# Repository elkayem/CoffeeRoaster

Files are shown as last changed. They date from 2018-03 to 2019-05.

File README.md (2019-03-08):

# COFFEE ROASTER

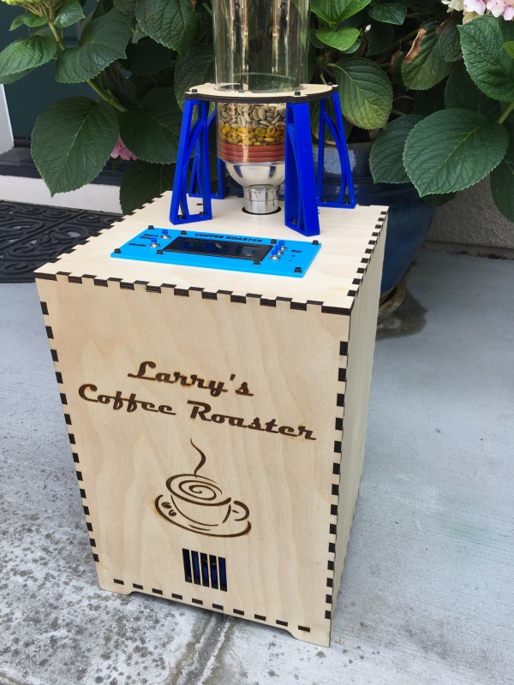
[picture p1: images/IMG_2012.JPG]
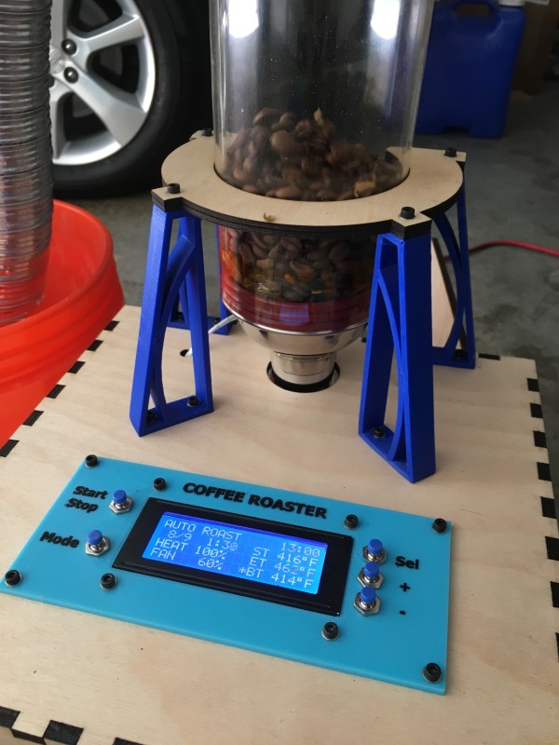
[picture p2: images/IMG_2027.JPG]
 

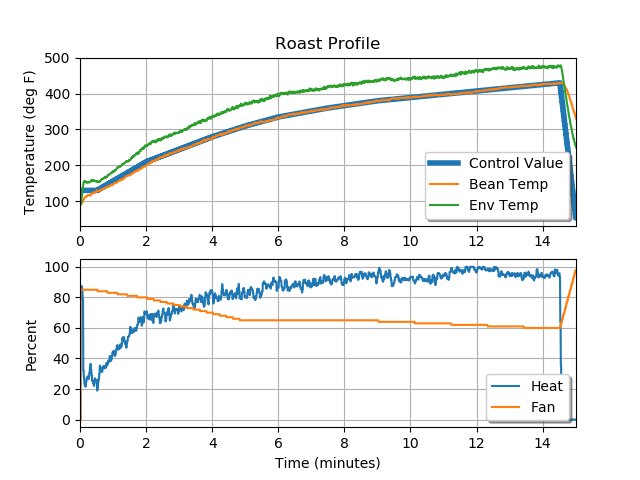
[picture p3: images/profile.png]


This repository contains the code for a PID controlled coffee roaster, run on a Teensy 3.5/3.6 development board.

A quick summary of the features:
* *Auto Mode* which will control the temperature (bean or environment) and fan speed to a settable profile.  
* *Manual Mode* where temperature and fan speed can be controlled in real time.
* Measured temperatures, set value, fan speed, and heater duty cycle saved to an SD card as a CSV file at 2 Hz while roasting.  See image above showing data from a roast.  I've also included a python script used to plot this data from the SD card.  The script requires the python module "matplotlib".  
* DC Fan PWM control.  (The MOSFET on the PCB can handle quite a bit of current.  I am using a 22 Amp, 260 Watt fan, and the MOSFET has additional headroom beyond that).    
* The roasting profile can be set as a sequence of up to 9 segments.  The set temperature and fan speed are linearly interpolated from one segment to the next.  This profile can be set and saved to EEPROM via the LCD screen interface.  
* Separate tuneable PID values for the environment temperature and bean temperature.  A tuning mode for each controller is available allowing one to monitor the step response and tune the gains in real time.
* (Optional) interface with [Artisan Roaster Scope](https://artisan-scope.org/).  The roast can be logged by Artisan in Auto or Manual mode, or even have Artisan control the set temperature and fan speed in Manual mode.  

I loosely based my roaster build off of a few of the fluid bed roasters over at the Home Roaster's forum using a Pyrex Bake-A-Round baking tube and inverted cocktail shaker lid.  For example, see Old Gear Head's fluid bed roaster design at: https://forum.homeroasters.org/forum/viewthread.php?thread_id=2207.   

Here are the parts needed for the electronics board:
* PCB (Order using gerber files in Eagle directory, or ask me and I'll send you one for a small amount.  Alternatively, the electronics can be soldered to a stripboard)
* Teensy 3.5 (or 3.6), $24.25 from pjrc.com + MicroSD card
* 2x MAX31855KASA+ thermocouple ICs ($5 each)
* 4x SMD ferrite beads (I used 470 ohms 0805 package)
* 3x BSS138 MOSFET transistors
* IRLB8721PBF MOSFET + heat sink (very important!!)
* 2N3904 transistor
* SB1245 Schottky diode
* 7805 5V regulator 
* Various resistors and capacitors (see schematic in Eagle directory)

Here are the additional parts I used:
* 20x4 character I2C LCD screen ($9 on eBay)
* Two K-type thermocouples
* Metal thermocouple probe shield (e.g., look for the 5mm x 50 mm thermocouple probe from Uxcell on Amazon, and cut off the end of the metal shield)
* Fotek SSR-40 DA Solid State Relay + Heat Sink ($12.50 on eBay)
* 12V, 25A power regulated switching power supply ($19 at eBay)
* Pyrex Bake-A-Round baking tube ($20 at eBay)
* Lid from Winco 16-oz coctail shaker, 1.5" and 3.5" diam ($7.50 at Amazon)
* 1.5" x 12" chrome tube ($10 at Amazon)
* HAS-043K 1700 Watt heating element ($22 at Amazon)
* Airhead "Air Pig" 12V, 22 Amp air pump ($42 at Amazon)
* 340 Silicone O-Rings 3.5" diam

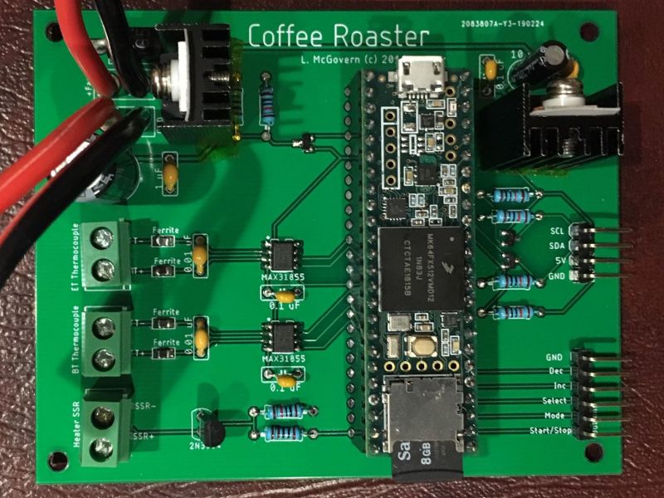
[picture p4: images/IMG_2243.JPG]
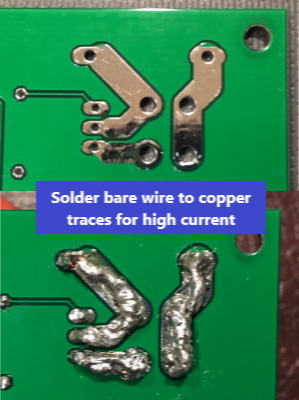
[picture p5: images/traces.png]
  

A schematic and PCB design (see Eagle folder) is included in this repository.  The Gerber files can be uploaded to a PCB manufacturer (e.g., JLCPCB, SchenZhen2U, or Seeed Studio), typically for a few dollars a board and a minimum order of 5-10 boards.  Alternatively, contact me and I can send you one (without components) at cost plus shipping.  The electronics can also be soldered to a breadboard.  If using a breadboard, you will also need two MAX31855 breakout boards from Adafruit, as well as a logic level converter for the I2C LCD communication.

The DC motor is driven by the 12V power supply, with PWM speed control from the microcontroller.  It is vitally important that a few small capacitors be soldered directly to the motor leads to reduce voltage noise on the DC power, otherwise the inevitable voltage spikes from the DC motor will reset the microcontroller in the middle of your roast.  Not good!  I used a 22 nF capacitor across the leads, and then two 10 nF capacitors from each lead directly to the motor housing.   

The 12V, 22 Amp DC motor I used draws a lot of current, so be sure to use beefy wires (e.g., 14 AWG) all the way to the MOSFET.  Be sure to use a heat sink on the IRLB8721PBF MOSFET.  The wide traces on the back of the PCB are inadequate to handle 22A.  I recommend laying down a heavy layer of solder directly to these traces.  Better yet, solder exposed 14 AWG wire directly to the traces.  See photos above.

I enclosed the DC motor in my own 3D printed case and threw away the pig shaped case on the Airhead "Air Pig".  I've included the 3D printed case model in this repository, which encloses the motor and is sealed with a 3.5" O-ring.  I'm sure the pig shaped case would work too, but don't use the corrugated hose which produces too much drag.  

Two temperature measurements are used.  I placed the Environment Temperature thermocouple close to the center of the chamber in the line of fire of the hot air, and the Bean Temperature probe off to the side and blocked from the upcoming air.  A metal thermocouple shield is used to hold the probes in place.  I purchased a thermocouple probe from Uxcell on Amazon that came with a metal shield, and sawed off the end of the metal shield.  I have included a photograph below showing the thermocouple placement, and a drawing as well.  The bean temperature thermocouple and wires are taped to the top of the thermocouple metal shield using Kapton tape, which allows this thermocouple to register the temperature of the beans descending along the side of the shaker lid, and outside of the stream of hot air.  

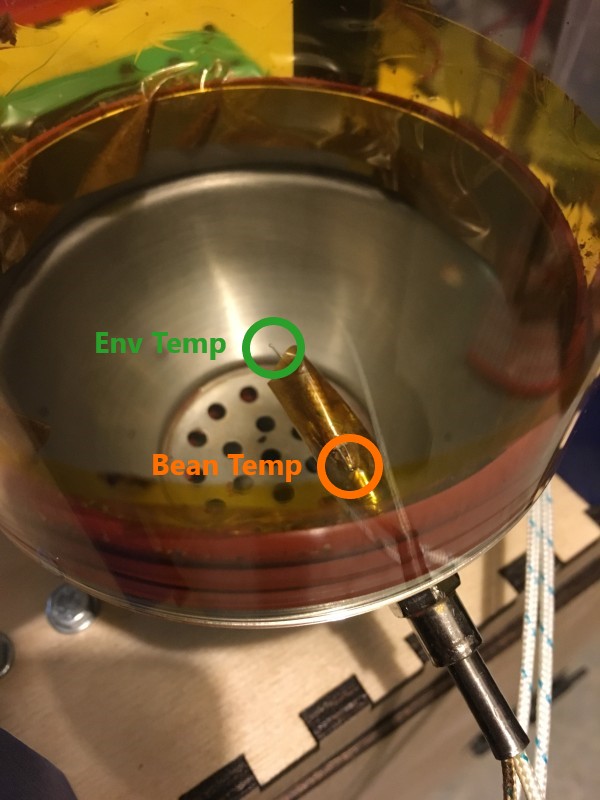
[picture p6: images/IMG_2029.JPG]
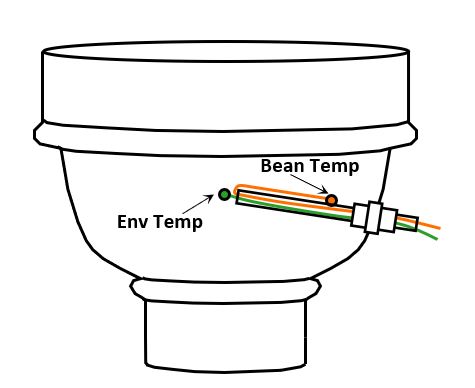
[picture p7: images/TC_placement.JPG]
 

I have also included a few 3D printed parts I used, which may be useful.  This repository includes a front panel for the LCD screen, and also the buttresses to hold the Bake-A-Round vertical. 

The plans for a 1/4" ply laser cut case are also included if you have access to a laser cutter.  Or build your own!  

# Artisan Roaster Scope Instructions
Artisan is not required for this roaster, as the Teensy firmware can already track a stored profile and save the roast data to an SD card without an external interface.  I still highly recommend Artisan as it includes additional visual analysis tools. 

**Important Note:** The USB port 5V power *must* be disconnected before attempting to interface with Artisan. There are several ways to do this, described at https://www.pjrc.com/teensy/external_power.html.  The simplest way is to disconnect the 5V pads apart on the bottom of the Teensy board.  I chose a different method in my roaster.  My roaster has a USB panel mount on the outside of the case, with an internal USB cable going from the panel mount to the Teensy.  Since this cable is permanently isntalled inside my case, I chose to clip the red wire inside the cable, sealing off the cut wire with shrink tube to prevent a short.  This avoids the need to modify the Teensy itself.

Coffee Roaster uses the same Artisan communication protocol as a TC4.  To use this Teensy code with Artisan, set up the device as a TC4 in Config>Device on the ET/BT tab.  Check the "Control" and "PID Firmware" checkboxes.  On the Extra Devices tab, set up the ArduinoTC4_34, ArduinoTC4_56 (Label 1 = Heater, Label 2 = Fan), and ArduinoTC4_78 (Label 1 = SV, Label 2 = Ambient).  Check the LCD 1, LCD 2, Curve 1, and Curve 2 checkboxes for ArduinoTC4_56 and _78, but uncheck for _34.  The YouTube video [Artisan Roaster Scope - Setup for TC4](https://youtu.be/0-Co-pXF2NM) walks through the setup procedure.

The above steps are sufficient for logging your roast with Artisan.  To control the roast using Artisan, check out the YouTube video [Artisan Roaster Scope - TC4 PID Control](https://youtu.be/ykuUCXhGAC4).  This video has four parts.  The two parts labeled "Background Follow TC4 PID" and "Ramp/Soak Profile TC4 PID" can be used with this code.  The "Artisan PID" variants are not currently supported.  

If using Artisan to control your roaster, you will also need to set up the DC Fan control. To do this, open the Config>Events dialog, change the first Event name to Fan, go to the Sliders tab, and set the Fan Action to Serial Command, and add the command "DCFAN;{}" to the selection box, without the quotes.  

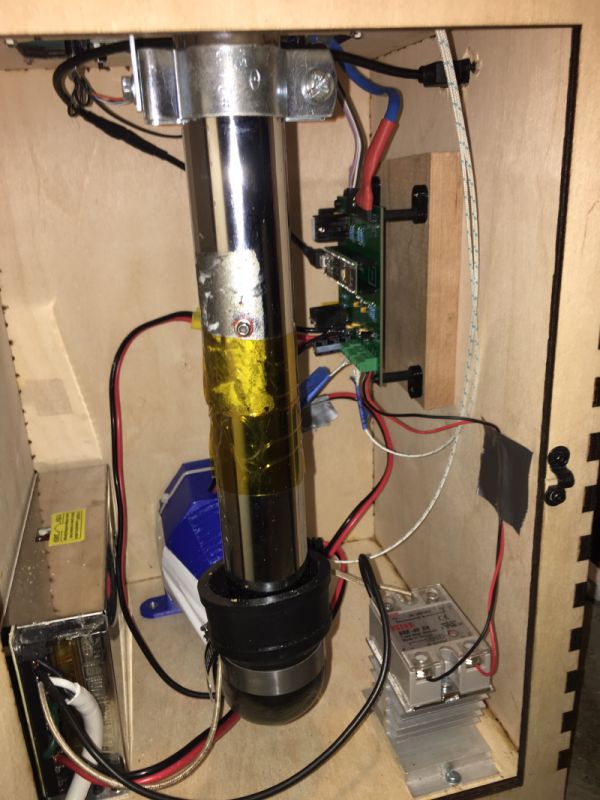
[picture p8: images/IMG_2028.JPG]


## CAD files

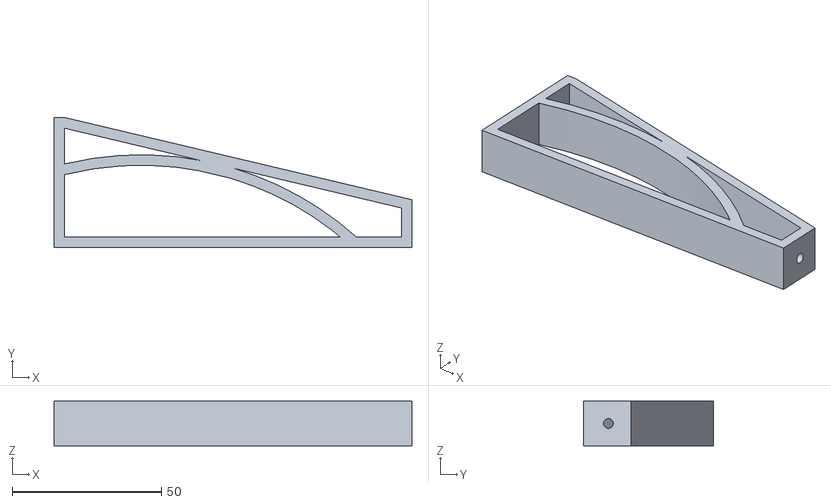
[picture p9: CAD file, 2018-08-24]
3D Printed Parts/buttress.stl
120.0 x 43.6 x 15.0

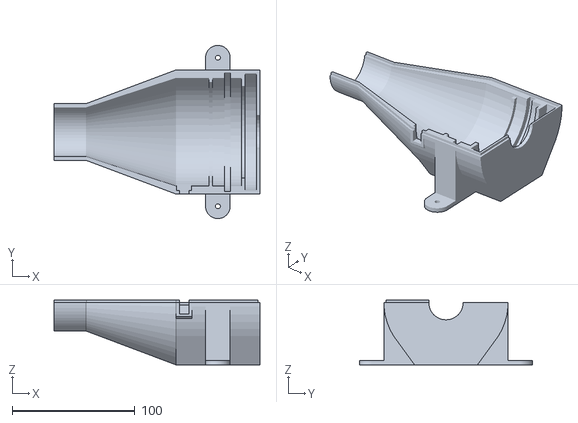
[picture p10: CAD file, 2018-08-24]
3D Printed Parts/fan_case_bottom.stl
167.5 x 140.8 x 52.5

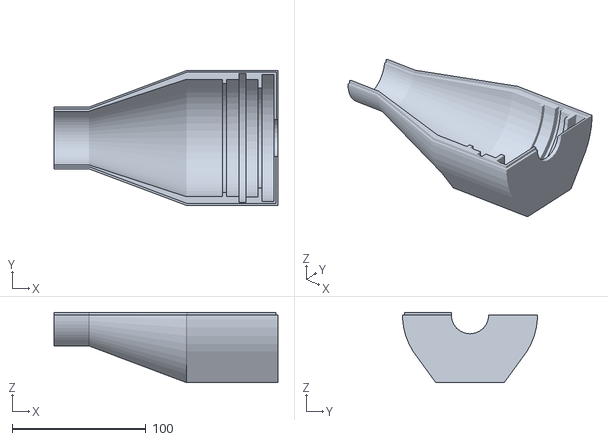
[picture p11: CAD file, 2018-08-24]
3D Printed Parts/fan_case_top.stl
167.5 x 100.8 x 52.5

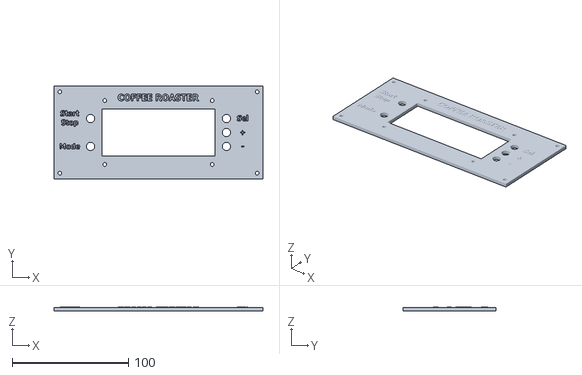
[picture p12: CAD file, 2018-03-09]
3D Printed Parts/panel.stl
180.0 x 80.0 x 3.45

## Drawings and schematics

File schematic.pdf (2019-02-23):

# BSS138 BSS138

# 1K ¹²³⁴⁵⁶⁷⁸⁹

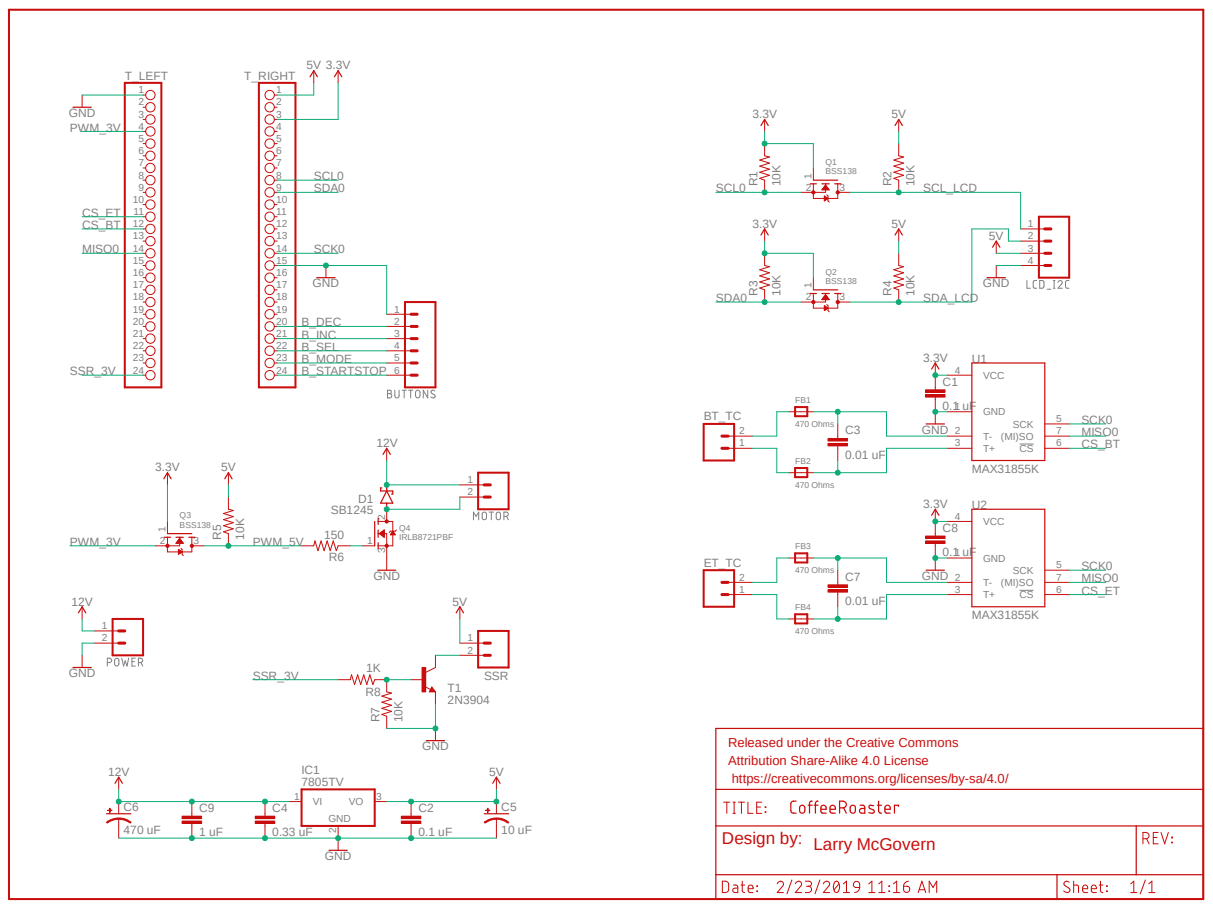
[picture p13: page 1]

Released under the Creative Commons
Attribution Share-Alike 4.0 License
https://creativecommons.org/licenses/by-sa/4.0/

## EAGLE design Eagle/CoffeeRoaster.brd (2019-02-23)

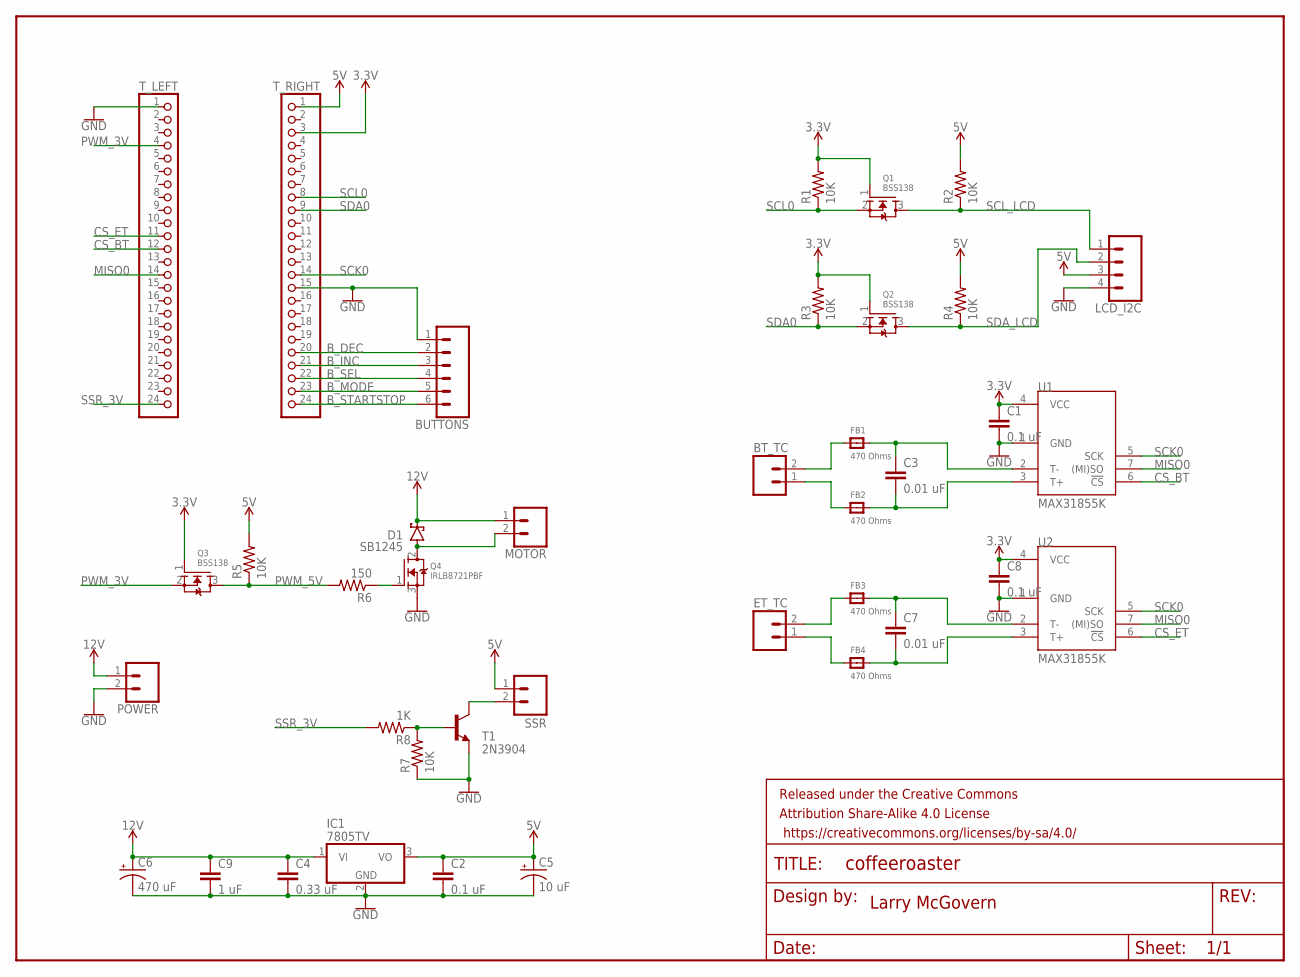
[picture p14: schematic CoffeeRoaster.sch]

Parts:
BT_TC: M025MM; SCREWTERMINAL-5MM-2
BUTTONS: CONN_06SILK_FEMALE_PTH; 1X06
C1, C2, C8: 0.1 uF; C050-025X075
C3, C7: 0.01 uF; C050-025X075
C4: 0.33 uF; C050-025X075
C5: 10 uF; E2,5-6
C6: 470 uF; E5-10,5
C9: 1 uF; C050-025X075
D1: SB1245; DO201T15
ET_TC: M025MM; SCREWTERMINAL-5MM-2
FB1, FB2, FB3, FB4: 470 Ohms; _0805
FRAME1: FRAME-LETTER; CREATIVE_COMMONS
IC1: 7805TV; TO220V
LCD_I2C: CONN_04; 1X04
MOTOR: CONN_02PTH4; 1X02_XTRA_BIG
POWER: CONN_02PTH4; 1X02_XTRA_BIG
Q1, Q2, Q3: BSS138; SOT23
Q4: IRLB8721PBF; TO220V
R1, R2, R3, R4, R5, R7: 10K; 0207/10
R6: 150; 0207/10
R8: 1K; 0207/10
SSR: M025MM; SCREWTERMINAL-5MM-2
T1: 2N3904; TO92
T_LEFT: PINHD-1X24; 1X24
T_RIGHT: PINHD-1X24; 1X24
U1, U2: MAX31855K; SO08

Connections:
3.3V: C1.1, C8.1, Q1.1 (G), Q2.1 (G), Q3.1 (G), R1.2, R3.2, T_RIGHT.3, U1.4 (VCC), U2.4 (VCC)
5V: C2.1, C5.+, IC1.3 (VO), LCD_I2C.3, R2.2, R4.2, R5.2, SSR.1, T_RIGHT.1
12V: C4.1, C6.+, C9.1, D1.C, IC1.1 (VI), MOTOR.1, POWER.1
B_DEC: BUTTONS.2, T_RIGHT.20
B_INC: BUTTONS.3, T_RIGHT.21
B_MODE: BUTTONS.5, T_RIGHT.23
B_SEL: BUTTONS.4, T_RIGHT.22
B_STARTSTOP: BUTTONS.6, T_RIGHT.24
CS_BT: T_LEFT.12, U1.6 (!CS)
CS_ET: T_LEFT.11, U2.6 (!CS)
GND: BUTTONS.1, C1.2, C2.2, C4.2, C5.-, C6.-, C8.2, C9.2, IC1.2 (GND), LCD_I2C.4, POWER.2, Q4.3 (S), R7.1, T1.3 (E), T_LEFT.1, T_RIGHT.15, U1.1 (GND), U2.1 (GND)
MISO0: T_LEFT.14, U1.7 ((MI)SO), U2.7 ((MI)SO)
MOT_NEG: D1.A, MOTOR.2, Q4.2 (D)
unnamed: Q4.1 (G), R6.1
unnamed: BT_TC.2, FB1.1
unnamed: ET_TC.2, FB3.1
unnamed: C3.1, FB1.2, U1.2 (T-)
unnamed: BT_TC.1, FB2.1
unnamed: C3.2, FB2.2, U1.3 (T+)
unnamed: C7.1, FB3.2, U2.2 (T-)
unnamed: ET_TC.1, FB4.1
unnamed: C7.2, FB4.2, U2.3 (T+)
unnamed: R7.2, R8.1, T1.2 (B)
unnamed: SSR.2, T1.1 (C)
PWM_3V: Q3.2 (S), T_LEFT.4
PWM_5V: Q3.3 (D), R5.1, R6.2
SCK0: T_RIGHT.14, U1.5 (SCK), U2.5 (SCK)
SCL0: Q1.2 (S), R1.1, T_RIGHT.8
SCL_LCD: LCD_I2C.1, Q1.3 (D), R2.1
SDA0: Q2.2 (S), R3.1, T_RIGHT.9
SDA_LCD: LCD_I2C.2, Q2.3 (D), R4.1
SSR_3V: R8.2, T_LEFT.24

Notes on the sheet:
Larry McGovern

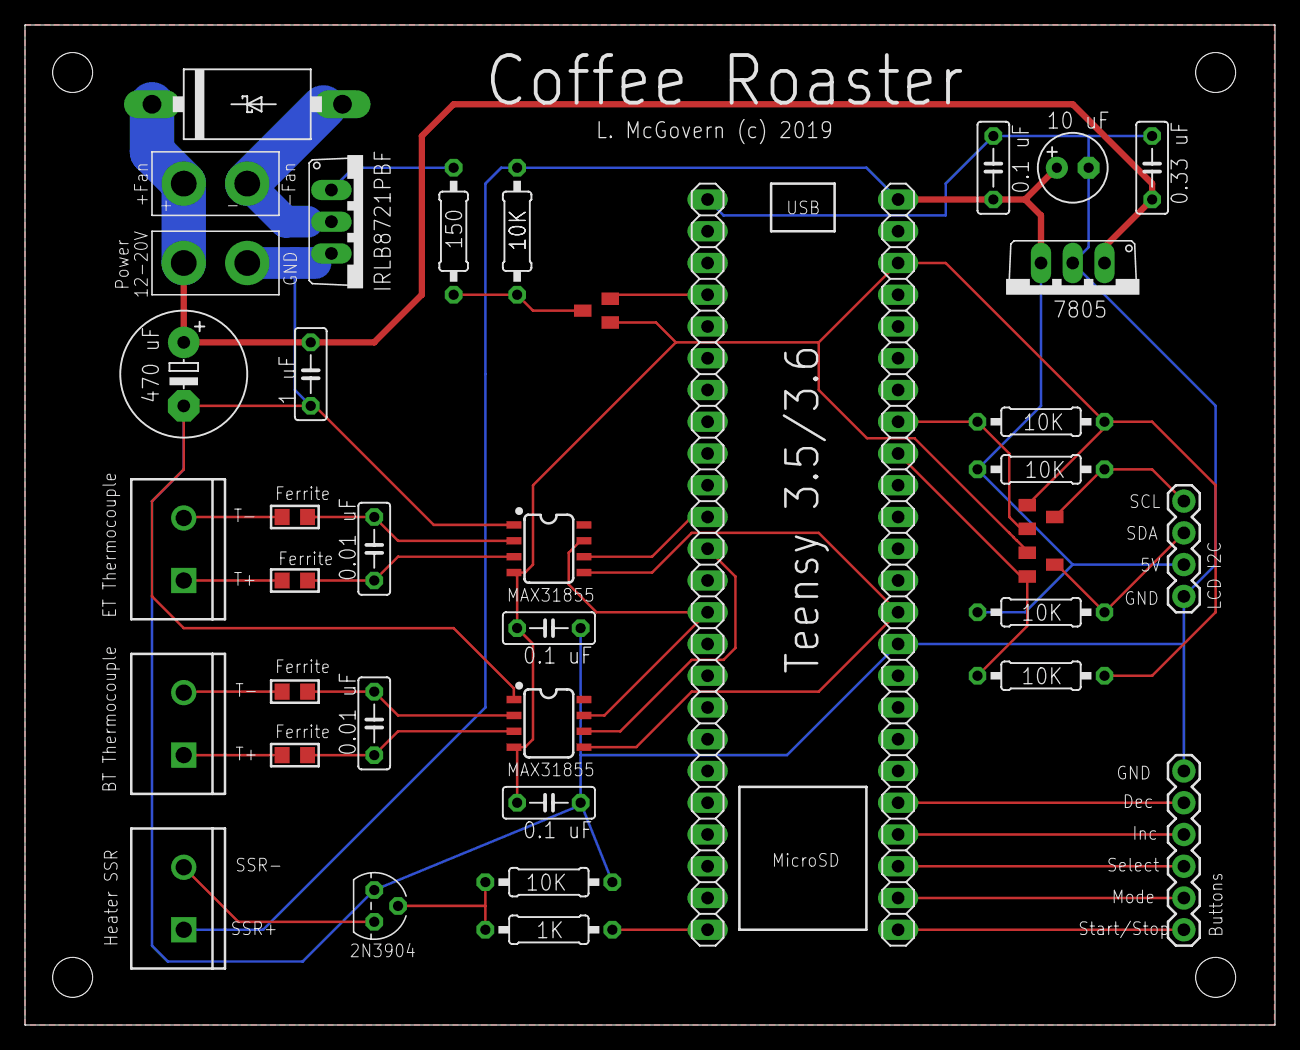
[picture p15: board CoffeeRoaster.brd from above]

Board: 2 copper layers, 100.0 x 80.0 mm, 40 parts (0 on the bottom side), 32 nets.

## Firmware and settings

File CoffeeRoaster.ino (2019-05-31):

/* 
 *    Coffee Roaster 
 *    Copyright (C) 2019  Larry McGovern
 *  
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
 *    This program is distributed in the hope that it will be useful,
 *    but WITHOUT ANY WARRANTY; without even the implied warranty of
 *    MERCHANTABILITY or FITNESS FOR A PARTICULAR PURPOSE.  See the
 *    GNU General Public License <http://www.gnu.org/licenses/> for more details.
 */
 
#include <SD.h>
#include <Wire.h>
#include <LiquidCrystal_I2C.h>
#include <SPI.h>
#include <EEPROM.h>
#include "Adafruit_MAX31855.h"
#include <Bounce2.h>

//
// Teensy 3.5/3.6 pin definitions
//
#define B_STARTSTOP 33
#define B_MODE      34
#define B_SEL       35
#define B_INC       36
#define B_DEC       37
#define FAN_PWM     2
#define SD_CS       BUILTIN_SDCARD
#define ENVTEMP_CS  9
#define BEANTEMP_CS 10
#define HEATER      32

Adafruit_MAX31855 beanTempSens(BEANTEMP_CS),envTempSens(ENVTEMP_CS);

LiquidCrystal_I2C lcd(0x27,20,4);  

Bounce startStopButton = Bounce();
Bounce modeButton = Bounce();
Bounce selButton = Bounce();
Bounce incButton = Bounce();
Bounce decButton = Bounce();

enum Modes {
  AUTO,
  MANUAL,
  SETTINGS,
  PIDTUNE_E,
  PIDTUNE_B,
  INIT
} mode;

enum EditVal {
  TEMP,
  FAN,
  CVAR,
  SEG,
  TIME,
  KP,
  KI,
  KD
} editVal;

enum ControlVar {
  ENV,
  BEAN
};

ControlVar controlVarMan = BEAN, controlVarAuto = BEAN;

// EEPROM Addresses
#define ADDR_KP_E 0  
#define ADDR_KI_E 2
#define ADDR_KD_E 4
#define ADDR_KP_B 6
#define ADDR_KI_B 8
#define ADDR_KD_B 10
#define ADDR_CVAR_MAN 12
#define ADDR_CVAR_AUTO 14
#define ADDR_SEG_TIME 16 // Address 16 - 33 (9 segments x 2 bytes)
#define ADDR_SEG_TEMP 34 // Addresses 34 - 51
#define ADDR_SEG_FAN  52 // Addresses 52 - 69

// Default gains.  These work well with a popcorn popper
#define KP_E_DEFAULT 100
#define KI_E_DEFAULT 150
#define KD_E_DEFAULT 200
#define KP_B_DEFAULT 100
#define KI_B_DEFAULT 150
#define KD_B_DEFAULT 200 

// Control gains are represented as integers ranging from 0 - 999, with LSBs below
#define KP_LSB 0.02  // LSB = 0.02% per deg, 20% per deg full range
#define KI_LSB 0.0005  // LSB = 0.0005% per deg-sec, 0.5% per deg-sec full range
#define KD_LSB 0.05   // LSB = 0.05% per deg/sec, 50% per deg/sec full range

#define BUFFERSIZE 6  // FIR Averaging filter for derivative filter.  Difference sample 6 and 1 for 5 second rolling average
class PidController {
  public:
  uint16_t Kp, Ki, Kd;
  void setPidGains(uint16_t Kp_in, uint16_t Ki_in, uint16_t Kd_in);
  double calcControl(double measTemp);
  void reset();
  
  private:
  double intErr = 0, errBuffer[BUFFERSIZE] = {0}; 
  int bIndx = 0; 
};

PidController envController, beanController;

// Profile global variables -- 9 segments used to define roasting profile for auto roast
int currentSeg = 1;
int currentSegTime;
double currentSetTemp, saveSetTemp;

// Default profile
uint16_t segTime[9] = {30,  90,  120, 60,  60,  90,  90,  330, 30}; // Time (in sec) for each segment
uint16_t segTemp[9] = {130, 210, 280, 310, 335, 360, 380, 430, 40}; // Final temperature (deg F) after completion of segment
uint16_t segFan[9]  = {85, 80, 70,  65,  65,  65,  65,  60,  100};  // Final fan speed (0 - 100) at completion of temperature

// Environment, bean, and ambient temperature measurements
double envTemp =  0; 
double beanTemp = 0;
double ambTemp = 0;

int envTempErrCtr = 0, beanTempErrCtr = 0; // Error counters
#define ERR_CTR_TIMEOUT 6

// Global variables for heat duty cycle (0-100) and fan duty cycle (0-100)
double heat = 0;
double fan = 0;

#define MIN_FAN_SPEED 50  // Minimum fan speed when heater is on, for safety

uint8_t heaterState;

unsigned long int secTimer = 0;

char filename[] = "LOG0000.CSV";
File logfile;
bool sdPresent = true;

/*
 * Setup
 */
void setup() {
  Serial.begin(115200);
  pinMode(B_STARTSTOP, INPUT_PULLUP);
  pinMode(B_MODE, INPUT_PULLUP);
  pinMode(B_SEL, INPUT_PULLUP);
  pinMode(B_INC, INPUT_PULLUP);
  pinMode(B_DEC, INPUT_PULLUP);

  pinMode(HEATER, OUTPUT);
  digitalWrite(HEATER, LOW);
  heaterState = LOW;
  
  startStopButton.attach(B_STARTSTOP);
  startStopButton.interval(25);

  modeButton.attach(B_MODE);
  modeButton.interval(25);

  selButton.attach(B_SEL);
  selButton.interval(25);

  incButton.attach(B_INC);
  incButton.interval(25);

  decButton.attach(B_DEC);
  decButton.interval(25);

  analogWriteFrequency(FAN_PWM, 10000); // 10 kHz PWM for fan control
  analogWriteResolution(12);  // 12-bit resolution on analogWrite commands
  setFanSpeed();

  lcd.init();
  lcd.setBacklight(HIGH);
  lcd.setCursor(0,1);
  lcd.print("Looking for SD Card");
  lcd.setCursor(0,3);
  lcd.print("Press SEL to bypass");

  while (SD.begin(SD_CS) != true)
  {
    if (digitalRead(B_SEL)== LOW) { // SEL pressed, bypass SD card
      sdPresent = false;
      break;
    }
    delay(10);
  }
  lcd.clear();
  
  lcd.setCursor(3, 0);
  lcd.print("COFFEE ROASTER");
  lcd.setCursor(9, 2);
  lcd.print("by");
  lcd.setCursor(3,3);
  lcd.print("Larry McGovern");

  delay(2000);
  
  // Load control gains
  bool useDefaults = false;
  uint16_t Kp = readEepromUint16(ADDR_KP_E);  
  uint16_t Ki = readEepromUint16(ADDR_KI_E);
  uint16_t Kd = readEepromUint16(ADDR_KD_E);

  // If all of the gains are zero or any are out of bounds, assume EEPROM isn't initialized
  // and use default values
  if (((Kp == 0) && (Ki == 0) && (Kd == 0)) || Kp > 999 || Ki > 999 || Kd > 999) {
    useDefaults = true;
    Kp = KP_E_DEFAULT;
    Ki = KI_E_DEFAULT;
    Kd = KD_E_DEFAULT;    
  }
  envController.setPidGains(Kp, Ki, Kd);
  
  Kp = readEepromUint16(ADDR_KP_B);  
  Ki = readEepromUint16(ADDR_KI_B);
  Kd = readEepromUint16(ADDR_KD_B);

  if (useDefaults || ((Kp == 0) && (Ki == 0) && (Kd == 0)) || Kp > 999 || Ki > 999 || Kd > 999) {
    useDefaults = true;
    Kp = KP_B_DEFAULT;
    Ki = KI_B_DEFAULT;
    Kd = KD_B_DEFAULT;    
  }
  beanController.setPidGains(Kp, Ki, Kd);

  // Load segment times and temperatures
  if (!useDefaults) {
    for (int i = 0; i < 9; i++) {
      segTime[i] = readEepromUint16(ADDR_SEG_TIME + 2*i);
      segTemp[i] = readEepromUint16(ADDR_SEG_TEMP + 2*i);
      segFan[i]  = readEepromUint16(ADDR_SEG_FAN + 2*i);
      if (segTime[i] > 900) segTime[i] = 30;
      if (segTemp[i] > 500) segTemp[i] = 100;
      if (segFan[i] > 100) segFan[i] = 100;
    }
  }
  currentSeg = 1;
  currentSegTime = segTime[0];
  currentSetTemp = (double)segTemp[0];
  saveSetTemp = currentSetTemp;

  // Load default control variable
  if (!useDefaults) {
    uint16_t cv = readEepromUint16(ADDR_CVAR_MAN); 
    if (cv == 0) controlVarMan = ENV;
    else controlVarMan = BEAN;
    cv = readEepromUint16(ADDR_CVAR_AUTO);
    if (cv == 0) controlVarAuto = ENV;
    else controlVarAuto = BEAN;
  }

  if (useDefaults) { // Save defaults to EEPROM
    mode = INIT;
    saveSettings();
  }

  mode = AUTO;
  editVal = FAN;
  
  lcd.clear();
  secTimer = millis();
  updateDisplay();
}

unsigned long elapsedTimeStart = 0;
float elapsedTime = 0.0;

bool roast = false, savedata = false, artisanPid = false, artisanPidPrev = false, endAutoRoast = false;;
int deltaFan;  // User adjust on fan speed made during auto roast

/*
 * Main Loop
 */
void loop() {
  static bool incState, decState;
  static unsigned long segTimeStart;
  static unsigned long incButtonPressTimeStamp1, decButtonPressTimeStamp1;
  static unsigned long incButtonPressTimeStamp2, decButtonPressTimeStamp2;
  static uint16_t fan0;
  static double setTemp0;
  uint16_t rate;

  getSerialCmd();  // Look for incoming serial commands from Artisan
  
  /*
   * Button Logic
   */
  startStopButton.update();
  modeButton.update();
  selButton.update();
  incButton.update();
  decButton.update();

  if (endAutoRoast) {  // Auto roast has ended.  We are waiting for the START/STOP button
                       // to be pushed to reset auto roast.  During this transition period,
                       // the fan speed can still be adjusted up and down, but all other 
                       // buttons are disabled
    if (startStopButton.fell()) { // START/STOP button was pushed
      endAutoRoast = false;
      fan = 0; 
      setFanSpeed();   // Turn off fan
      lcd.clear();
      updateDisplay(); // and update display
      return;          // Return and skip any other button logic
    }
  } // end if(endAutoRoast)
  
  if (startStopButton.fell() ||            // Called when start/stop button pressed,
      (artisanPid != artisanPidPrev)) {    // or Artisan PID On or Off command received in Manual or PID TUNE mode
    if (artisanPid != artisanPidPrev) { // Received a command from Artisan
      artisanPidPrev = artisanPid;
      if (roast == artisanPid) return;  // Roast state was already in correct state, do nothing
      roast = artisanPid;
    }
    else { // Button was pushed
      roast = !roast; // Toggle roast state
      artisanPid = roast;  // Treat a start/stop button push as if the command came from Artisan
      artisanPidPrev = artisanPid; 
    }
    if (roast) {    // If starting new roast
        elapsedTimeStart = millis();
        if (sdPresent) {
          for (uint16_t i = 0; i < 9999; i++) {  // Pick a new file name
            filename[3] = i / 1000 + '0';
            filename[4] = i / 100 % 10 + '0';
            filename[5] = i / 10 % 10 + '0';
            filename[6] = i % 10 + '0';
            if (!SD.exists(filename)) {
              // only open a new file if it doesn't exist
              logfile = SD.open(filename, FILE_WRITE);
              break;  
            }
        }
        logfile.println("Time, Control Temp, Env Temp, Bean Temp, Heat, Fan");
        logfile.flush();
      }
      if (mode == AUTO) {
        currentSetTemp = (double)segTemp[0];
        currentSegTime = segTime[0];
        fan0 = segFan[0];
        deltaFan = 0;
        setTemp0 = (double)segTemp[0];
        currentSeg = 1;
        segTimeStart = elapsedTimeStart; 
      }
    }
    else {  // End the roast
      heat = 0;  // Turn heat off, but leave fan running
      envController.reset();
      beanController.reset();
      if (sdPresent) logfile.close();
      
      if (mode == AUTO) { // Reset auto roast to initial settings
        endAutoRoast = true;  
        currentSeg = 1;  
        currentSetTemp = (double)segTemp[0];
        currentSegTime = segTime[0];   
        lcd.clear();
        updateDisplay();
      }
    }
  }  // end if (startStopButton.fell())

  if (modeButton.fell()) {  // Switch Modes
    if (!roast && !endAutoRoast) { // Only switch modes if not roasting and not in the endAutoRoast transition
      saveSettings(); // Save settings to EEPROM when switching modes
      switch (mode) {
        case AUTO:
          mode = MANUAL;
          editVal = TEMP;
          break;
        case MANUAL:
          mode = SETTINGS;
          editVal = SEG;
          saveSetTemp = currentSetTemp;
          currentSeg = 1;
          currentSegTime = segTime[0];
          currentSetTemp = (double)segTemp[0];
          break;
        case SETTINGS:
          mode = PIDTUNE_E;
          editVal = KP;
          currentSetTemp = saveSetTemp;
          break;
        case PIDTUNE_E:
          mode = PIDTUNE_B;
          break;
        case PIDTUNE_B:
          mode = AUTO;
          editVal = FAN;
          break;
        default:
          break;
      }
      lcd.clear();
      updateDisplay();
    }
  } // end if (modeButton.fell())

  if (selButton.fell()) {  // Make new selection (MANUAL and SETTINGS modes)
    switch (mode) {
      case MANUAL:
        if (editVal == TEMP)  editVal = FAN;
        else if (editVal == FAN) editVal = CVAR;
        else editVal = TEMP;
        break;
      case SETTINGS:
        if (editVal == SEG) editVal = TIME;
        else if (editVal == TIME) editVal = TEMP;
        else if (editVal == TEMP) editVal = FAN;
        else if (editVal == FAN) editVal = CVAR;
        else editVal = SEG;
        break;
      case PIDTUNE_E:
      case PIDTUNE_B:
        if (editVal == KP) editVal = KI;
        else if (editVal == KI) editVal = KD;
        else if (editVal == KD) editVal = TEMP;  
        else if (editVal == TEMP) editVal = FAN;  
        else if (editVal == FAN) editVal = KP;  
        break;  
      default:  
        break;
    }
    updateDisplay();
  } // end if (selButton.fell())

  if (incButton.fell()) { // Increment button was pushed.  Increment selection
      if (editVal == CVAR) {
        if (mode == SETTINGS) controlVarAuto = (controlVarAuto == ENV ? BEAN : ENV);
        else controlVarMan = (controlVarMan == ENV ? BEAN : ENV);
        envController.reset();
        beanController.reset();
        savedata = true;
        updateDisplay();
      }
      else if (editVal == SEG) {
        currentSeg++;
        if (currentSeg > 9) currentSeg = 9;
        currentSegTime = segTime[currentSeg-1];
        currentSetTemp = (double)segTemp[currentSeg-1];
        updateDisplay();
      }
      else {  // editVal = TEMP, FAN, TIME, KP, KI, or KD
        incState = true;
        incButtonPressTimeStamp1 = millis();
        incButtonPressTimeStamp2 = incButtonPressTimeStamp1;       
      }
  } // end if (incButton.fell())
  else if (incButton.read() == HIGH) { // Button has been released
      incState = false;
  }

  if (incState) { // used when increment button pressed while editVal = TEMP, FAN, TIME, KP, KI, or KD
    if (millis() - incButtonPressTimeStamp1 >= 3000)  // If button depressed for longer than 3 seconds, then increment faster
      rate = 50;
    else
      rate = 500;
    if (millis() - incButtonPressTimeStamp2 >= rate) {
      lcd.setCursor(0,0);
      incDecSelection(1);
      incButtonPressTimeStamp2 = millis();
    }
  }
  
  if (decButton.fell()) { // Decrement button was pushed.  Decrement selection
      if (editVal == CVAR) {
        if (mode == SETTINGS) controlVarAuto = (controlVarAuto == ENV ? BEAN : ENV);
        else controlVarMan = (controlVarMan == ENV ? BEAN : ENV);
        envController.reset();
        beanController.reset();
        savedata = true;
        updateDisplay();
      }
      else if (editVal == SEG) {
        currentSeg--;
        if (currentSeg < 1) currentSeg = 1;
        currentSegTime = segTime[currentSeg-1];
        currentSetTemp = (double)segTemp[currentSeg-1];
        updateDisplay();
      }
      else { // editVal = TEMP, FAN, TIME, KP, KI, or KD
        decState = true;
        decButtonPressTimeStamp1 = millis();
        decButtonPressTimeStamp2 = decButtonPressTimeStamp1;       
      }
  }
  else if (decButton.read() == HIGH) { // Button has been released
      decState = false;
  }

  if (decState) { // used when increment button pressed while editVal = TEMP, FAN, TIME, KP, KI, or KD
    if (millis() - decButtonPressTimeStamp1 >= 3000)
      rate = 50;
    else
      rate = 500;
    if (millis() - decButtonPressTimeStamp2 >= rate) {
      incDecSelection(-1);
      decButtonPressTimeStamp2 = millis();
    }
  }

  /*
   *  Read sensors and update display.  If roasting, update control and save to SD Card
   */

  static bool firstMeas = false;  // Temperatures measured twice every second and averaged
  static double envTempMeas1 = NAN, beanTempMeas1 = NAN;
  static double envTempAve = 0, beanTempAve = 0;

  if ((millis() - secTimer >= 500) && (firstMeas == false)) { // First measurement, called at the half-second mark
    
    readTempSensors();
    
    if (envTempErrCtr == 0)  envTempMeas1 = envTemp;    
    else envTempMeas1 = NAN;  
    
    if (beanTempErrCtr == 0) beanTempMeas1 = beanTemp;    
    else beanTempMeas1 = NAN;  

    updateDisplay();
    updateSD();
    
    firstMeas = true;
  }
  
  if (millis() - secTimer >= 1000) { // Second measurement and duty cycle update, called at the 1 second mark 
    secTimer = millis();
    
    // If the heat duty cycle > 0 and we're roasting,
    // then turn on heater at beginning of 1 second interval
    if ((heat > 0) && roast) heaterState = HIGH;
    else  heaterState = LOW;
    digitalWrite(HEATER, heaterState);  
    
    readTempSensors();
    
    if (!isnan(envTempMeas1) && (envTempErrCtr == 0) ) // Two valid measurements
      envTempAve = 0.5 * (envTempMeas1 + envTemp);    // Calculate average
    else
      envTempAve = envTemp;  // Otherwise, set to last valid measurement

    if (!isnan(beanTempMeas1) && (beanTempErrCtr == 0) ) // Two valid measurements
      beanTempAve = 0.5 * (beanTempMeas1 + beanTemp);    // Calculate average
    else
      beanTempAve = beanTemp;  // Otherwise, set to last valid measurement

    // Calculate feedback control
    heat = 0;  // Heat off by default
    if (roast) {  // If we're roating, calculate temperature set values and heater/fan duty cycles
      if (mode == AUTO) { // Auto roast follows segment profiles
        currentSegTime = (int)segTime[currentSeg-1] - (int)(millis() - segTimeStart)/1000; // Counts down in seconds from segTime to 1
        if (currentSegTime < 1) { // If we reach 0, it is time to move to the next segment
          setTemp0 = (double)segTemp[currentSeg-1];
          fan0 = segFan[currentSeg-1];
          currentSeg++;

          // End the roast if we are at the end of the 9th segment, or the next segment length is 0
          if (currentSeg > 9) endAutoRoast = true;
          else if (segTime[currentSeg-1] == 0) endAutoRoast = true;
          
          if (endAutoRoast == true) { // End the roast, and display endAutoRoast transition screen
            roast = false;
            heat = 0;    // Turn heater off
            fan = fan0;  // Turn fan speed to the final segment fan speed value
            setFanSpeed();
            currentSeg = 1;  // Reset auto roast to initial settings
            currentSetTemp = (double)segTemp[0];
            currentSegTime = segTime[0];   
            envController.reset();
            beanController.reset();
            if (sdPresent) logfile.close();
            lcd.clear();
            updateDisplay();
            return;
          }
          currentSegTime = segTime[currentSeg-1];
          segTimeStart = millis(); 
        }  // end if (currentSegTime < 1)

        // Linearly interpolate the current set temperature and fan duty cycle 
        currentSetTemp = setTemp0 + ((double)segTemp[currentSeg-1] - setTemp0) * (double)(millis() - segTimeStart)/(1000*(double)segTime[currentSeg-1]);
        fan = deltaFan + (int)((double)fan0 + ((double)segFan[currentSeg-1] - (double)fan0) * (double)(millis() - segTimeStart)/(1000*(double)segTime[currentSeg-1]));
      }
      if ((mode == PIDTUNE_E) || ((mode == MANUAL) && (controlVarMan == ENV)) || ((mode == AUTO) && (controlVarAuto == ENV))) { // Env temp control
        if (envTempErrCtr < ERR_CTR_TIMEOUT) {
          heat = envController.calcControl(envTempAve);
        }
      }
      else { // Bean temp control
        if (beanTempErrCtr < ERR_CTR_TIMEOUT) {
          heat = beanController.calcControl(beanTempAve);
        }
      }
    }
    setFanSpeed();
    updateDisplay();
    updateSD();
    firstMeas = false;
  }

  heaterDutyCycleOff(); 
}

/*
 * Save settings to EEPROM.  This is called whenever switching modes.
 */
void saveSettings() {
  uint16_t cv;
  if(savedata || (mode == INIT)) { // Save if one of the settings has changed, or if initializing EEPROM
    if ((mode == MANUAL) || (mode == INIT)) {
      if (controlVarMan == ENV)  cv = 0;
      else cv = 1;
      writeEepromUint16(ADDR_CVAR_MAN, cv);
    }
    if ((mode == SETTINGS) || (mode == INIT)) {
      if (controlVarAuto == ENV)  cv = 0;
      else cv = 1;
      writeEepromUint16(ADDR_CVAR_AUTO, cv);
      for (int i = 0; i < 9; i++) {
         writeEepromUint16(ADDR_SEG_TIME + 2*i, segTime[i]);
         writeEepromUint16(ADDR_SEG_TEMP + 2*i, segTemp[i]);
         writeEepromUint16(ADDR_SEG_FAN  + 2*i, segFan[i]);
      }
    }
    if ((mode == PIDTUNE_E) || (mode == INIT)) {
      writeEepromUint16(ADDR_KP_E, envController.Kp);
      writeEepromUint16(ADDR_KI_E, envController.Ki);
      writeEepromUint16(ADDR_KD_E, envController.Kd);
    }
    if ((mode == PIDTUNE_B) || (mode == INIT)) {
      writeEepromUint16(ADDR_KP_B, beanController.Kp);
      writeEepromUint16(ADDR_KI_B, beanController.Ki);
      writeEepromUint16(ADDR_KD_B, beanController.Kd);
    }
    if (mode != INIT) {
      lcd.clear();
      lcd.setCursor(1,1);
      lcd.print("Saving Settings...");
      delay(1000);
    }
  }
  savedata = false;
}

/*
 * heaterDutyCycleOff() -- Check to see if heater needs to be turned off
 */
void heaterDutyCycleOff() {
  uint16_t dc = (uint16_t)(10*heat);  // Duty cycle integer from 0 - 1000
  if (heat >= 100.0) return;  // Will leave heater on no matter what
  if ((millis() - secTimer >= dc) && (heaterState == HIGH)) { 
    heaterState = LOW;
    digitalWrite(HEATER, LOW);
  }
}

/*
 * readTempSensors() -- Read temperature sensors
 */
void readTempSensors() {

  ambTemp = 0.5 * (envTempSens.readInternal() + beanTempSens.readInternal());
  ambTemp = 32.0 + 1.8 * ambTemp;
  
  double envTempC = envTempSens.readCelsius();
  if (isnan(envTempC)) {  
    envTempErrCtr++;
  }
  else {
    envTemp = 32.0f + 1.8f * envTempC;
    envTempErrCtr = 0;
  }
  
  double beanTempC = beanTempSens.readCelsius();

  if (isnan(beanTempC)) {  
    beanTempErrCtr++;
  }
  else {
    beanTemp = 32.0 + 1.8 * beanTempC;
    beanTempErrCtr = 0;
  }
  
  if (envTempErrCtr >= ERR_CTR_TIMEOUT) envTemp = NAN;
  if (beanTempErrCtr >= ERR_CTR_TIMEOUT) beanTemp = NAN;
}
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

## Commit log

2018-02-28 Add 2nd pid loop
2018-03-06 Derivative FIR filter
2018-03-09 Add README and additional files
    [Popper mount.stl, panel.stl]
2018-03-17 modify set temperature data type
2018-08-24 Updated for new roaster design.
    [Popper mount.stl, buttress.stl, fan_case_bottom.stl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]
2019-02-23 Updates for Teensy 3.5
    [CoffeeRoaster.brd, CoffeeRoaster.sch]

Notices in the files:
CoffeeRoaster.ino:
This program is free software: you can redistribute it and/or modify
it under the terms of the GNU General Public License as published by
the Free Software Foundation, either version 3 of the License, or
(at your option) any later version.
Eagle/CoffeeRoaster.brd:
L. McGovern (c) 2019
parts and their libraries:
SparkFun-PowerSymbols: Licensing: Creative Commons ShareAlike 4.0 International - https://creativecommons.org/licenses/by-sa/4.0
